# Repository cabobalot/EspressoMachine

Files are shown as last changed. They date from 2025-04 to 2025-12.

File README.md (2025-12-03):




Gagginator - A Modified Gaggia Classic Machine
==============================================
https://mrfangao.github.io/EspressoMachine/index.html

The Gagginator is a small open souce project created by The Bean Team that aims to enhance the Gaggia Classic espresso machine by replacing its traditional temperature and pressure control systems with a smart, configurable system for greater customization and consis-
tency for its users.

The project focuses on three main improvements: upgrading the temperature system with a PID controller for precise, user-adjustable temperature settings; implementing a pressure control system to allow for active profiling of extraction pressure; and adding a minimalist visual display to show real-time temperature, pressure, and brew time for easy monitoring. The system will also support custom brew settings and preset profiles based on the user’s preferences. 

## Table of Contents

- [Features](#key-features)
- [Hardware Requirements](#hardware-requirements)
- [Repository Structure](#repository-structure)
- [Files in this Repository](#files-in-this-repository)
- [Installation](#installation)
- [Usage](#usage)
- [Contributing](#contributing)
- [License](#license)

Key Features
-----------------

- **PID Temperature Control**: Precise, user-adjustable temperature control
- **Active Pressure Profiling**: Dynamic control of brew pressure during the brew cycle
- **Real-Time Monitoring**: Live display of temperature, pressure, and brew time.
- **Custom Brew Profiles**: Save and recall personalized brewing settings.
- **Web Interface**: Local webpage for detailed brew data visualization
- **Minimalist OLED Display**: Clear at-a-glance brewing information

Hardware Requirements
--------------------

- Gaggia Classic espresso machine
- ESP32-WROOM-32 dev board
- Additional components (see BOM)

<!--TODO-->

## Repository Structure
```
gagginator/
├── README.md                    
├── Espresso Machine/            
│   ├── data/
│   │   └── brewData.html      
│   ├── bitmaps.h               
│   ├── dataWebPage.cpp    
│   ├── dataWebPage.h     
│   ├── EspressoMachine.h   
│   ├── EspressoMachine.ino     
│   ├── menu.cpp     
│   ├── menu.h         
│   ├── pins.h                  
│   ├── pressure_control.cpp   
│   ├── pressure_control.h 
│   ├── pressure_sensor.cpp    
│   ├── pressure_sensor.h 
│   ├── psm.cpp    
│   ├── psm.h             
│   ├── temp_sensor.cpp      
│   ├── temp_sensor.h   
│   ├── tempControl.cpp    
│   ├── tempControl.h     
│   └── timingTestDebug.h       
├── Gaggia Schematic/                                  
```

Files in this Repository
------------------------

#### README.md 

You are currently here.

#### Espresso Machine

This folder holds the required code to run the Gagginator. All the `.cpp` and `.ino` files require their supporting `.h` files in order to run.

| File | Description |
| --- | --- |
| `data`  | A folder containing `brewData.html` for the data webpage  |
| `bitmaps.h`  | Holds the animations for coffee graphics  |
| `dataWebPage.cpp`  | The locally hosted webpage displaying brew parameters  |
| `EspressoMachine.ino` | The Main loop  of the Gagginator  |
| `menu.cpp`  | Handles all the screen and interface with the user |
| `pins.h`  | Defines the pin locations on the ESP32  |
| `pressure_control.cpp`  | Controls the pressure of the machine  |
| `pressure_sensor.cpp`  | Collects data from the pressure sensor  |
| `psm.cpp`  | Implements a PSM controller using zero-cross detection |
| `temp_sensor.cpp`  | Collects data from the temperature sensor  |
| `tempControl.cpp`  | Controls the temperature of the machine |
| `timingTestDebug.h`  | Debug code to track timing of code chunks  |

Simply copy all of the files from this folder into your project.

#### Gaggia Schematic

The circuit diagram for wiring the hardware components for the Gagginator.

Installation 
---------------

### Prerequisites

- Arduino IDE (version 1.8.x or 2.x)
- ESP32 board support package
- Required libraries:
  - Adafruit SSD1306 (for OLED display)
  - Wifi (depricated)
  <!--all other stuff sensors... TODO-->

### Steps

1. **Clone the repository**
```bash
   git clone https://github.com/yourusername/gagginator.git
   cd gagginator
```

2. **Install required libraries**
   - Open Arduino IDE
   - Navigate to Sketch → Include Library → Manage Libraries
   - Install required dependencies listed above

3. **Configure hardware pins**
   - Follow `pins.h` to match the ESP32 board and wiring configuration
   - Verify sensor pin assignments

4. **Upload the code**
   - Open `Espresso Machine/EspressoMachine.ino` in Arduino IDE (or have it configured in VSCode)
   - Select your ESP32 board from Tools → Board
   - **ENSURE** memory partition scheme is 3MB/SPIFFS no OTA
   - Select the correct COM port
   - Click Upload

5. **Upload web interface files**
   - Install the ESP32 filesystem uploader plugin
   - Upload the `data/` folder to SPIFFS/LittleFS

## Usage

### First-Time Setup

1. Power on the modified Gagginator
2. <!-- TODO -->

5. (Optional) Connect to the Gagginator WiFi access point
Navigate to the web interface at `http://192.168.4.1`

### Basic Operation

- **Temperature Control**: Use the menu to set your desired brew temperature
- **Pressure Profiling**: Select or create custom pressure profiles
- **Monitoring**: View real-time parameters on the OLED display
- **Data Logging**: Access detailed brew statistics via an browser under the AP "Gagginator" at the IP address of `192.168.4.1`.

#### Safety Notes

⚠️ **WARNING**: This modification involves working with  electricity, high temperatures, and hot water! Only attempt if you have appropriate electrical and mechanical knowledge. Improper installation may result in electric shock, fire, or equipment damage, and even injury or death

Contributing
---------------

This project is fully developed as of the release of this project. However contributions are welcome, and further modifications are at your descretion. To do so, please:

1. Fork the repository
2. Create a feature branch (`git checkout -b feature/improvement`)
3. Commit your changes (`git commit -am 'add your feature'`)
4. Push to the branch (`git push origin feature/improvement`)
5. Open a Pull Request

License
-----------

This project is open source. Specific license TBD

## Acknowledgments

The Bean Team would like to thank Samuel Bona for suffering statistical shambles and chemistry chaos. We also thank our Lord and Savior, the coffee god: James Hoffmann.

## Contact

For questions, issues, or contributions, please open an issue on GitHub.

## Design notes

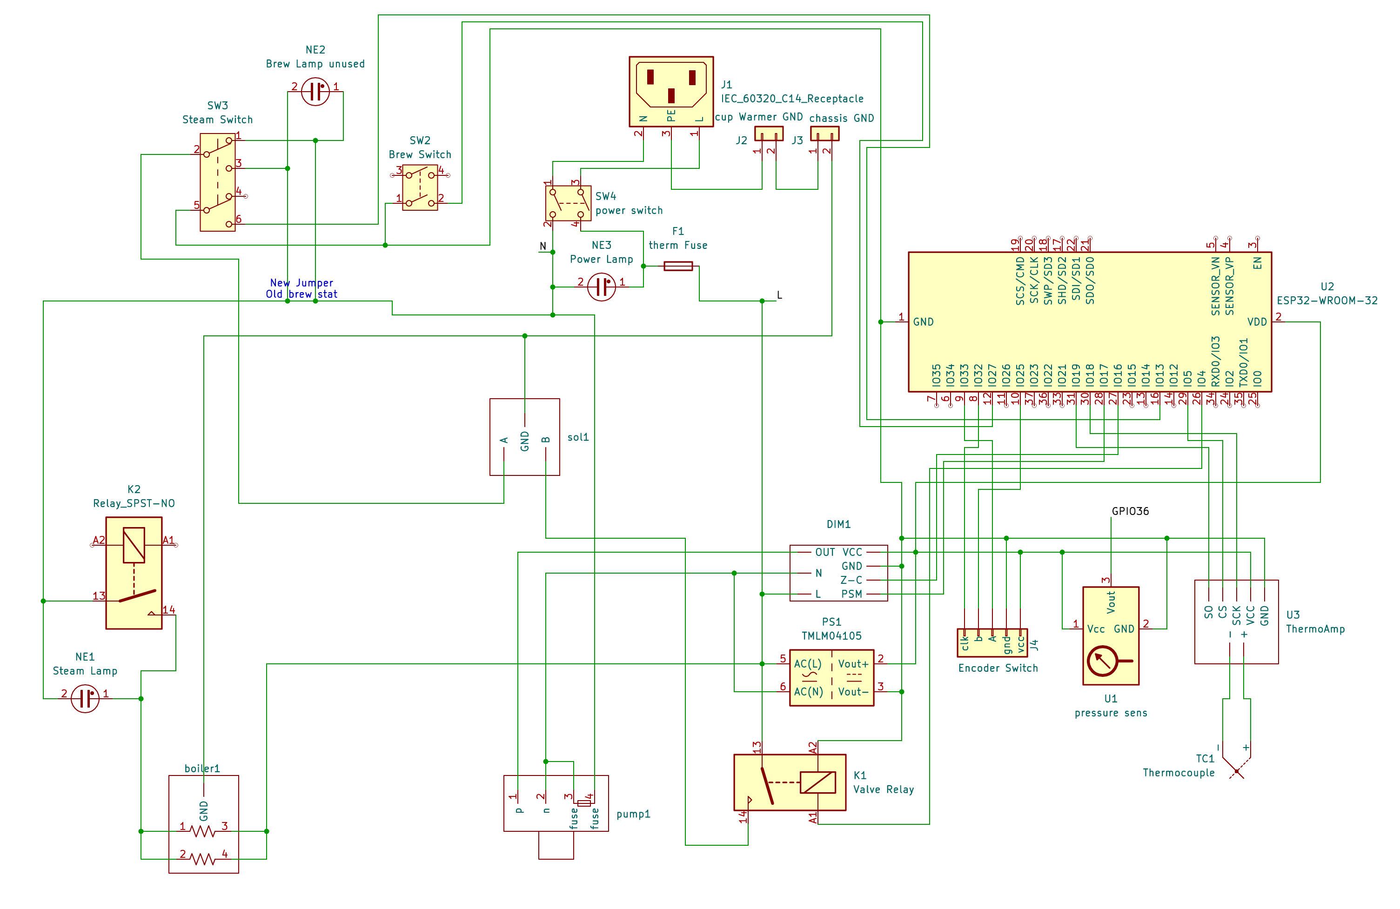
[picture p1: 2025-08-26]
schematic.png

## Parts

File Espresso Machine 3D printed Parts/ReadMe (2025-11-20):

This folder contains the stl and bambulab files used in this project.

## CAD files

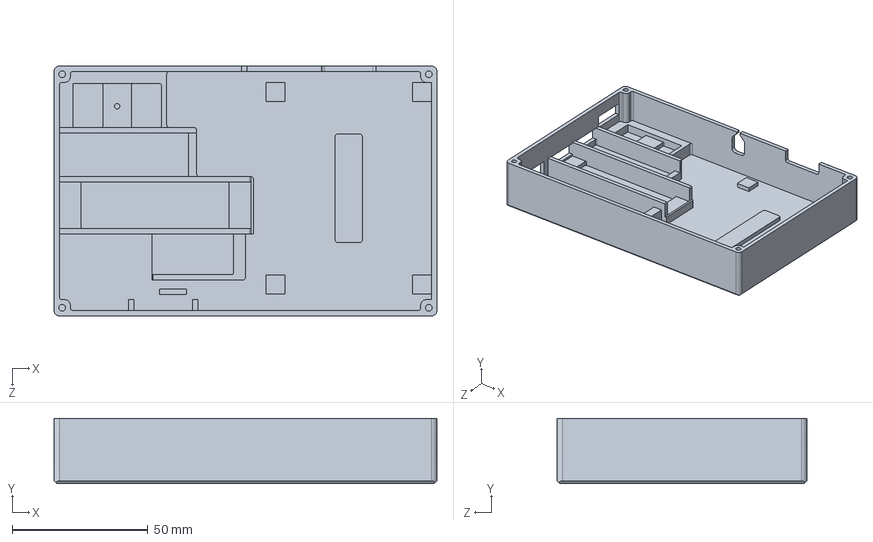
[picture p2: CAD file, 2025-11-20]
Espresso Machine 3D printed Parts/ESP32 Housing Final.SLDPRT
141.0 x 24.0 x 92.0 mm

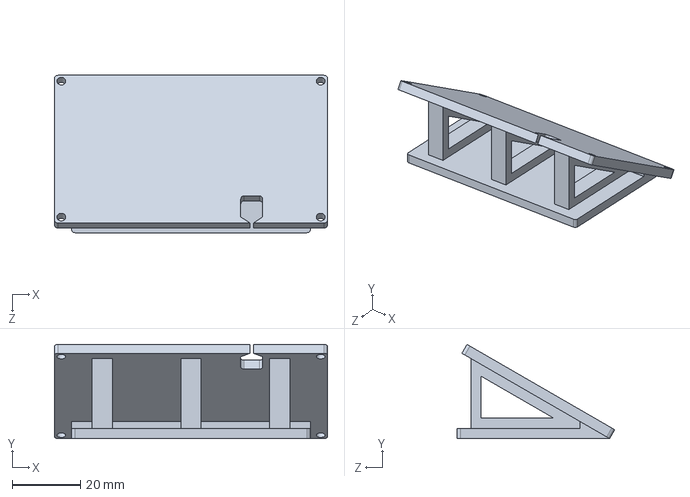
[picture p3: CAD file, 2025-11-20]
Espresso Machine 3D printed Parts/Mount for Knob and Screen Enclousure Final.SLDPRT
80.0 x 27.6 x 46.2 mm

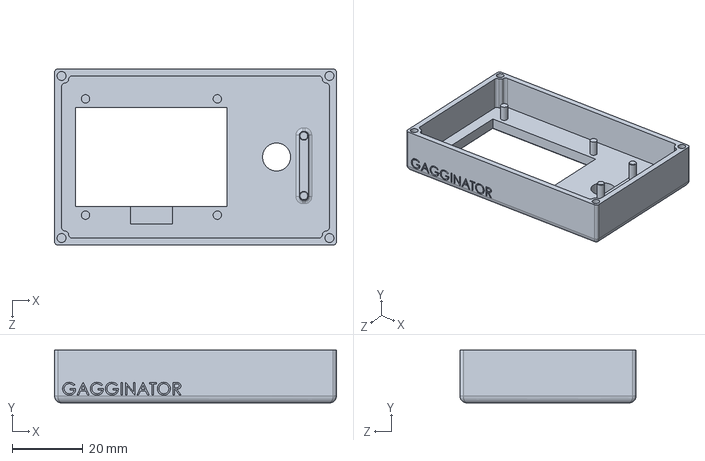
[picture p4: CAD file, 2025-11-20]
Espresso Machine 3D printed Parts/Knob and Screen Enclosure Final.SLDPRT
80.0 x 15.0 x 50.0 mm

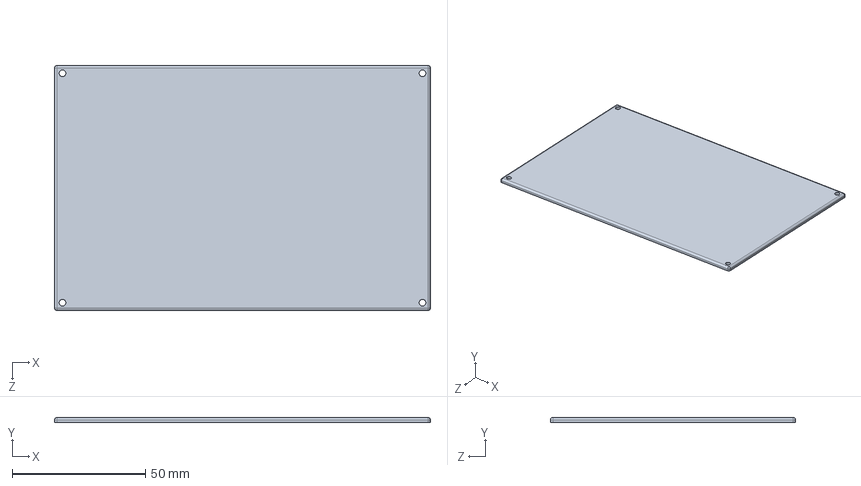
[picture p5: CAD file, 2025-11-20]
Espresso Machine 3D printed Parts/ESP32 Housing Lid Final.SLDPRT
141.0 x 2.00 x 92.0 mm

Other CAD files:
Espresso Machine 3D printed Parts/ESP32 Housing Final.STL
Espresso Machine 3D printed Parts/ESP32 Housing Lid Final.STL
Espresso Machine 3D printed Parts/Knob and Screen Enclosure Final.STL
Espresso Machine 3D printed Parts/Mount for Knob and Screen Enclousure Final.STL

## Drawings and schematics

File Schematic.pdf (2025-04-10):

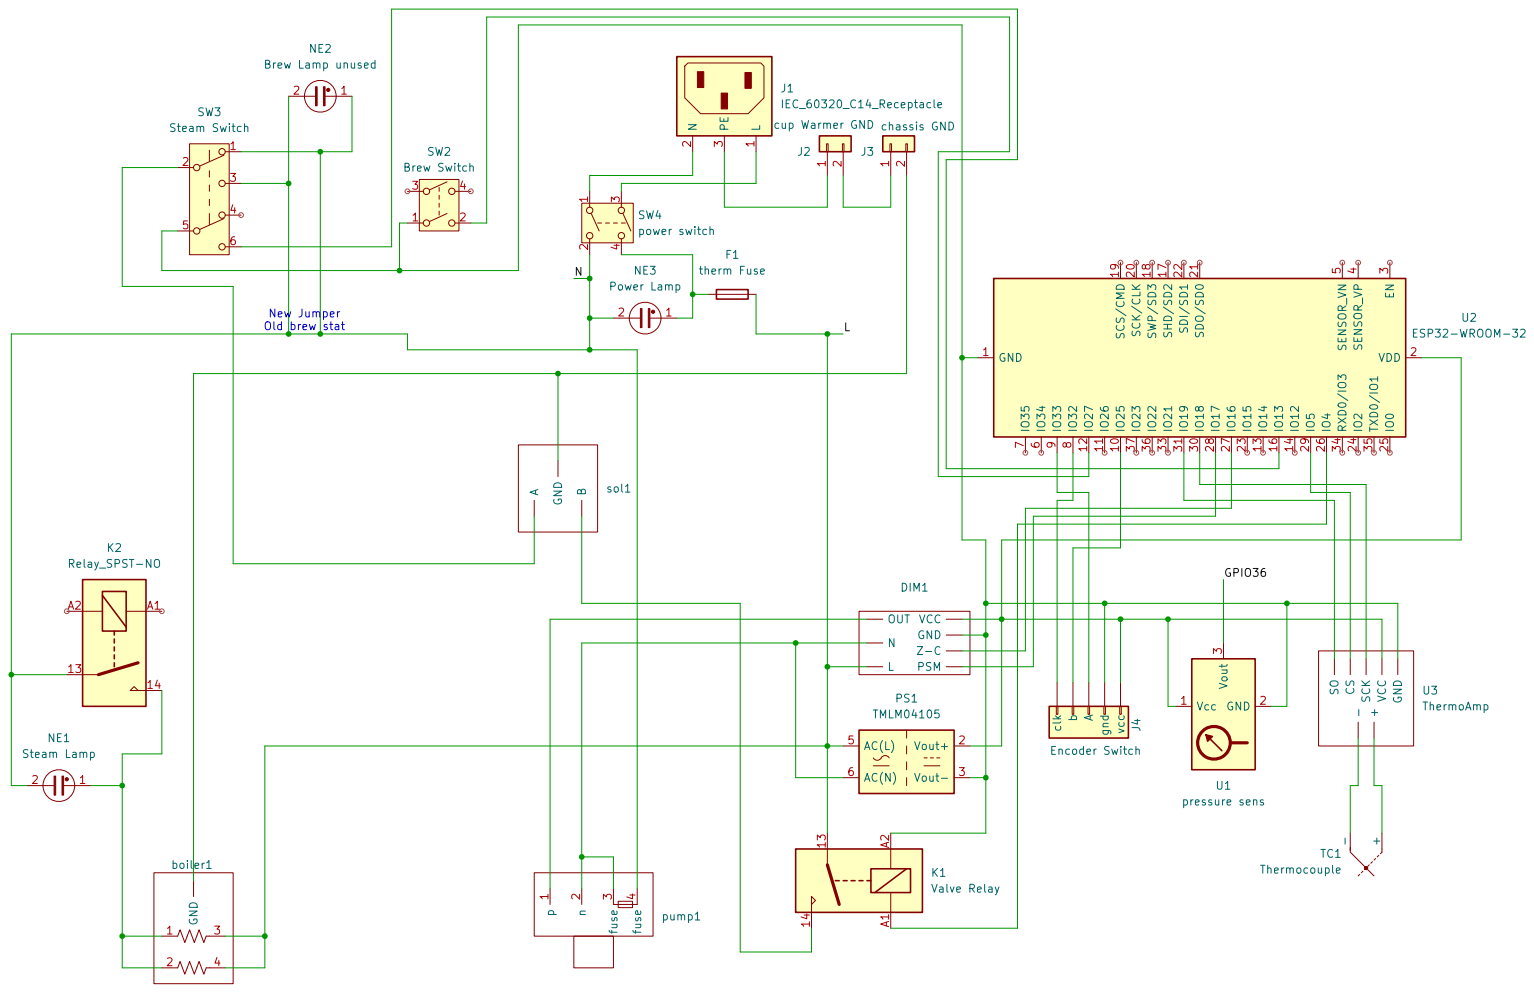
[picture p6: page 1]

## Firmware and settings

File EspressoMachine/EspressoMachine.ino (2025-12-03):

#include "Menu.h"
#include "bitmaps.h"
#include "pressure_sensor.h"
#include "temp_sensor.h"
#include "pins.h"
#include "pressure_control.h" 
#include "tempControl.h" 
#include "dataWebPage.h"
#include "EspressoMachine.h"

#include "timingTestDebug.h"


#define TEMPERATURE_OFFSET 7 // stock calibration offset

TemperatureSensor tempSensor;
PressureControl pc(5, 0.0, 0.1);
// also test in steam mode

TaskHandle_t mainTask;
TaskHandle_t uiTask;
TaskHandle_t screenShowTask;

void mainLoop(void * pvParameters);
void uiLoop(void * pvParameters);
void screenShowLoop(void * pvParameters);

static volatile float targetTemperature = 95;
static volatile float targetPressureBrew  = 120.0f;
static volatile uint8_t steamPercentage = 2;  // 1-128, default 2%
static volatile float currentTemperature = 0;
static volatile float currentPressure = 0;

static volatile float preinfusePressure = 25;
static volatile unsigned long preinfuseTime = 10;

// Brew mode pressure control: record brew start time for switching between preinfusion and normal pressure
static volatile unsigned long brewStartTimeMs = 0;
static volatile float currentTargetPressure = 0.0f;  // Currently used target pressure (for serial output)


static volatile MachineState machineState = IDLE_STATE;


void setup() {
  Serial.begin(115200);

  if (!menu.begin()) { // doing this here so we have serial if it fails
    Serial.println(F("SSD1306 allocation failed"));
    for(;;);
  }
  
  dataWebPage::init(); // I hope this doesnt care which core it happens on

  xTaskCreatePinnedToCore(uiLoop, "uiLoop", 10000, NULL, 1, &uiTask, 1);
  xTaskCreatePinnedToCore(mainLoop, "mainLoop", 10000, NULL, 1, &mainTask, 1);
  xTaskCreatePinnedToCore(screenShowLoop, "screenShowLoop", 10000, NULL, 1, &screenShowTask, 0);
}

void screenShowLoop(void * pvParameters) {
  for(;;) {
    menu.show();
    vTaskDelay(50 / portTICK_PERIOD_MS); // 20 FPS max
  }
}

void uiLoop(void * pvParameters) {
  // --- debounce state ---
  static bool     lastBrewRaw  = false,  brewStable  = false;
  static bool     lastSteamRaw = false,  steamStable = false;
  static uint32_t brewEdgeMs   = 0,      steamEdgeMs = 0;
  const  uint16_t DEBOUNCE_MS  = 30;

  menu.beginInput(PIN_KNOB_ROTATE_A, PIN_KNOB_ROTATE_B, PIN_KNOB_BUTTON); // pins an interrupt on this core

  pinMode(PIN_SWITCH_BREW, INPUT_PULLUP);
  pinMode(PIN_SWITCH_STEAM, INPUT_PULLUP);

  // Load saved settings
  menu.loadSettings();

  for(;;) {
    // ===================== UI input & rendering =====================

    menu.pollInput();
    
    int step = menu.consumeStep();
    if (step != 0) menu.moveSelection(step > 0);
    if (menu.consumeClick()) menu.select();

    // Targets from UI
    // Select corresponding temperature based on current mode
    if (machineState == STEAM_STATE) {
      targetTemperature = menu.getTargetTemperatureSteam() + TEMPERATURE_OFFSET;
    } else {
      // BREW_STATE, IDLE_STATE, HOT_WATER_STATE use brew temperature
      targetTemperature = menu.getTargetTemperatureBrew() + TEMPERATURE_OFFSET;
    }
    targetPressureBrew  = menu.getTargetPressureBrew();
    steamPercentage = menu.getSteamPercentage();
    preinfusePressure   = menu.getPreinfPressure(); 
    preinfuseTime       = menu.getPreinfTimeSec();

    // Live values back to UI
    menu.setCurrentTemperature(currentTemperature - TEMPERATURE_OFFSET);
    menu.setCurrentPressure(currentPressure);

    // ===================== Switch handling (level-based, both edges) =====================
    // Active-low hardware switches: LOW = pressed
    bool rawBrew  = !digitalRead(PIN_SWITCH_BREW);
    bool rawSteam = !digitalRead(PIN_SWITCH_STEAM);
    uint32_t now  = millis();

    // --- Brew debounce ---
    if (rawBrew != lastBrewRaw) { lastBrewRaw = rawBrew; brewEdgeMs = now; }
    if ((now - brewEdgeMs) >= DEBOUNCE_MS && rawBrew != brewStable) {
      brewStable = rawBrew;
    }

    // --- Steam debounce ---
    if (rawSteam != lastSteamRaw) { lastSteamRaw = rawSteam; steamEdgeMs = now; }
    if ((now - steamEdgeMs) >= DEBOUNCE_MS && rawSteam != steamStable) {
      steamStable = rawSteam;
    }

    // --- Unified decision (priority: BOTH -> WATER, else single) ---
    MachineState nextState = machineState;
    if (brewStable && steamStable) {
      nextState = HOT_WATER_STATE;            // Water mode: both keys pressed
    } else if (brewStable) {
      nextState = BREW_STATE;                 // Only Brew key pressed
    } else if (steamStable) {
      nextState = STEAM_STATE;                // Only Steam key pressed
    } else {
      nextState = IDLE_STATE;                 // Neither pressed
    }

    // --- Apply transition once (and set the correct page) ---
    if (nextState != machineState) {
      machineState = nextState;

      switch (machineState) {
        case BREW_STATE:
          brewStartTimeMs = millis();  // Record brew start time
          menu.setState(BREW_PAGE);
          menu.resetBrewAnimation();
          break;
        case STEAM_STATE:
          menu.setState(STEAM_PAGE);
          break;
        case HOT_WATER_STATE:
          menu.setState(WATER_PAGE);          // Both keys pressed -> enter Water page
          break;
        case IDLE_STATE:
        default:
          menu.setState(MAIN_MENU);
          break;
      }
    }

    // yield();
    vTaskDelay(20 / portTICK_PERIOD_MS); // 

  }
}

void mainLoop(void * pvParameters) {
  //temperature
  tempControl::init();
  //presure
  pinMode(PIN_PRESSURE_SENSE, INPUT);
  pc.init(PIN_DIMMER_CONTROL, PIN_DIMMER_ZERO_CROSS); // this pins an interrupt to this core

  // init
  pc.setAlwaysOff();

  pinMode(PIN_SOLENOID, OUTPUT);
  digitalWrite(PIN_SOLENOID, LOW);


  for(;;) {
    switch (machineState) {
    case IDLE_STATE:
      pc.setAlwaysOff();
      digitalWrite(PIN_SOLENOID, LOW);
      currentTargetPressure = 0.0f;
      break;
    case BREW_STATE:
      {
        // Calculate brew elapsed time (milliseconds)
        unsigned long brewElapsedMs = millis() - brewStartTimeMs;
        unsigned long preinfuseTimeMs = preinfuseTime * 1000;  // Convert to milliseconds
        
        // Use preinfusion pressure (20 PSI) for first 5 seconds, then use 70 PSI
        if (brewElapsedMs < preinfuseTimeMs) {
          currentTargetPressure = preinfusePressure;  // 20 PSI
        } else {
          currentTargetPressure = targetPressureBrew;  // Switch to 70 PSI after 5 seconds
        }
        
        pc.setSetpoint(currentTargetPressure);
        digitalWrite(PIN_SOLENOID, HIGH);
      }
      break;
    case STEAM_STATE:
      // Steam mode uses percentage for direct control, doesn't use PID
      pc.setPercentage(steamPercentage);
      digitalWrite(PIN_SOLENOID, LOW);
      // currentTargetPressure is for display, can be set to percentage value (optional)
      currentTargetPressure = (float)steamPercentage;  // Display percentage value
      break;
    case HOT_WATER_STATE:
      pc.setAlwaysOn();
      digitalWrite(PIN_SOLENOID, LOW);
      break;
    }

    tempControl::setSetpoint(targetTemperature); // screen returns a different temperature for each mode
    currentTemperature = tempControl::getTemperature();

    currentPressure = pc.getPressure();

    pc.update();

    tempControl::update();

    dataWebPage::update(currentTemperature - TEMPERATURE_OFFSET, currentPressure, targetTemperature - TEMPERATURE_OFFSET, currentTargetPressure, machineState);
    
    static unsigned long timeLastPrint = 0;
    if (millis() - timeLastPrint >= 1000) {
      timeLastPrint = millis();

      // Serial.printf("temp:%.1f, tempset:%.1f, pres:%.1f, pressSet:%.1f\r\n", currentTemperature, targetTemperature, currentPressure, targetPressure);


      // Serial.print(">temp:");
      // Serial.print(currentTemperature, 2);
      // Serial.print(",tempset:");
      // Serial.print(targetTemperature, 2);
      // Serial.print(",pres:");
      // Serial.print(currentPressure, 2);
      // Serial.print(",pressSet:");
      // Serial.print(targetPressureBrew, 2);
      // Serial.print(",targetPress:");
      // Serial.println(currentTargetPressure, 2);

      // Serial.print("UI core: ");
      // Serial.print(xTaskGetCoreID(uiTask));
      // Serial.print(" main core: ");
      // Serial.println(xTaskGetCoreID(mainTask));

    }

    // pretty sure we dont need a taskDelay here but maybe
    yield();
  }
}

void loop() {

}

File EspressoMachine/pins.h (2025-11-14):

#ifndef PINS_H
#define PINS_H

#define PIN_TEMP_SENS_SCK 18 
#define PIN_TEMP_SENS_CS  5
#define PIN_TEMP_SENS_SO  19

#define PIN_PRESSURE_SENSE 36 // analog input

#define PIN_DIMMER_ZERO_CROSS 16
#define PIN_DIMMER_CONTROL    17 // triac output

#define PIN_SCREEN_SDA 21
#define PIN_SCREEN_SCL 22

#define PIN_KNOB_BUTTON 32
#define PIN_KNOB_ROTATE_A 33
#define PIN_KNOB_ROTATE_B 25

#define PIN_SOLENOID 4
#define PIN_HEATER   26

#define PIN_SWITCH_BREW  27
#define PIN_SWITCH_STEAM 13

#endif

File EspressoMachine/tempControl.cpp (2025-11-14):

#include <Arduino.h>
#include "tempControl.h"
#include <PID_v1.h> // PID library
#include "driver/mcpwm.h" // ESP32 PWM library
#include "soc/mcpwm_periph.h"
#include "pins.h"

#define PWM_FREQ 1 // Frequency of PWM pin (1Hz)

// Static variables to hold current temp and target
static double currentTemp = 0.0;
static double setpoint = 0.0;
static double outputDuty= 0.0;

// PID varibles
static double Kp = 7.0, Ki = 1.5, Kd = 4.0;

// Delay between updates (1 sec)
unsigned long prevMillis = 0;
const unsigned long interval = 1000;

// PID object from library
static PID tempPID(&currentTemp, &outputDuty, &setpoint, Kp, Ki, Kd, DIRECT);

/*
Setup to allow for the temperature control to change the temperature
*/
void tempControl::init() {

  // PID setup
  tempPID.SetMode(AUTOMATIC);
  tempPID.SetOutputLimits(0, 100);  // clamp output

  // PWM setup
  mcpwm_timer_set_resolution(MCPWM_UNIT_0, MCPWM_TIMER_1, 60000);

  // Config to setup the PWM for the ESP32
  mcpwm_gpio_init(MCPWM_UNIT_0, MCPWM1A, PIN_HEATER);
  mcpwm_config_t pwm_config;
  pwm_config.frequency = PWM_FREQ;
  pwm_config.cmpr_a = 0.0;
  pwm_config.counter_mode = MCPWM_UP_COUNTER;
  pwm_config.duty_mode = MCPWM_DUTY_MODE_0;
  mcpwm_init(MCPWM_UNIT_0, MCPWM_TIMER_1, &pwm_config);
}

/*
Setter for the desired setpoint
*/
void tempControl::setSetpoint(float temp){
  setpoint = temp;
}

/*
Setter for the current temperature
*/ 
void tempControl::setCurrentTemp(float temp){
  currentTemp = temp;
}

/*
Controls and updates the duty cycle to reach the setpoint
*/
void tempControl::setTemperature(float tempSetpoint) {
  // PID controller
  if(tempPID.Compute()) {
    // Changes the duty cycle
    mcpwm_set_duty(MCPWM_UNIT_0, MCPWM_TIMER_1, MCPWM_OPR_A, outputDuty);
  }
}

/*
Getter for temperature
*/
float tempControl::getTemperature() {
  return currentTemp;
}

/*
Getter for setpoint
*/ 
float tempControl::getSetpoint(){
  return setpoint;
}

/*
At given intervals gets the current temperature and updates it until the 
set temperature is reached.
*/
void tempControl::update() {

    unsigned long currMillis = millis();

    if(currMillis - prevMillis >= interval) { // Delay 
      prevMillis = currMillis;

      currentTemp = TemperatureSensor::getTemperature(); // Grab the current temperature
      
      tempControl::setTemperature(setpoint); // Reach that temperature

    }
}

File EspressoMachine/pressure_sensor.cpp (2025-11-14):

#include <Arduino.h>
#include "pressure_sensor.h"
#include"pins.h"

// Sensor parameters
const int pressurePin = PIN_PRESSURE_SENSE;
const float sensorMinVoltage = 0.5;
const float sensorMaxVoltage = 4.5;

const float pressureMin = 0.0;
const float mPaMax = 1.2;

// ESP32 specific parameters
const float maxVoltage = 3.3;
const float adcResolution = 4095.0; // 12 bit resolution (0-3.3V)

// Voltage divider parameters
const float voltageDividerRatio = 1.515;

// Averaging constant
static const uint8_t NUM_READINGS = 20;
static uint16_t ringBuf[NUM_READINGS];  // ~40B
static uint8_t  head = 0;               // Next location to write to
static uint8_t  count = 0;              // Current number of samples (<= NUM_READINGS)
static uint32_t sumAdc = 0;             // Run and prevent overflow

/*
Averages the pressure readings coming in from the sensor
*/
static inline uint16_t readAveragedAdc() {
  uint16_t newv = (uint16_t)analogRead(pressurePin);
  if (count < NUM_READINGS) {
    // Buffer not full, accumulate directly
    sumAdc += newv;
    ringBuf[head++] = newv;
    count++;
    if (head == NUM_READINGS) head = 0;
  } else {
    // Buffer full, pop the old value, add the new one in
    uint16_t oldv = ringBuf[head];
    sumAdc += newv;
    sumAdc -= oldv;
    ringBuf[head] = newv;
    head++;
    if (head == NUM_READINGS) head = 0;
  }

  // Calculate the current average (rounded)
  uint32_t denom = (count == 0) ? 1 : count;
  uint16_t avg = (uint16_t)((sumAdc + denom / 2) / denom);
  return avg;
}

/*
Handles the calculations to take voltage sensor readings into a pressure format.
*/
int calculatePressure() {
  int i = 0;
  int rawTotalValue = 0;
  static int avgValue;
  static float bar = 0;
  static float psi = 0;
  static unsigned long prevMs_ = 0;

  const unsigned long now = millis();

  // update every 3ms
  if (now - prevMs_ >= 3) {
    prevMs_ = now;

    avgValue = readAveragedAdc();
    // Convert ADC value to ESP pin voltage (0-3.3V)
    float measuredVoltage = (avgValue / adcResolution) * maxVoltage;
    
    // Calculate the actual sensor output voltage (accounting for voltage divider)
    float actualVoltage = measuredVoltage * voltageDividerRatio;
    
    // Scale the reading to actual pressure in MPa
    float pressureRange = mPaMax - pressureMin;
    float voltageRange = sensorMaxVoltage - sensorMinVoltage;
    
    float pressure = ((actualVoltage - sensorMinVoltage) * pressureRange / voltageRange) + pressureMin; // in mPa
    
    // Ensure pressure is within expected range (sanity check)
    pressure = constrain(pressure, pressureMin, mPaMax);

    // Conversion to bar and PSI
    bar = pressure * 10;
    psi = pressure * 145.038;
  }
  return psi; // PSI is default, but mPa or bar is valid.
}

const int printToPlotter = 0; // 1 to plot, 0 to print metadata

/*
Prints data either to a serial plotter or directly into the console
*/
void printAvgData(float avgSensorValue, float avgPsi, float avgBar, float avgVoltage) {
  if (printToPlotter) {
    Serial.println(avgPsi); // fill with desired measurement
  }
  else { // Print to console
    Serial.print("Raw ADC: ");
    Serial.println(avgSensorValue);
    Serial.print("Measured Voltage: ");
    Serial.println(avgVoltage, 3);
    Serial.print("Bar: ");
    Serial.println(avgBar, 3);
    Serial.print("PSI: ");
    Serial.println(avgPsi, 3);
  }
}

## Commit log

2025-04-02 Working Arduino Pressure Sensor Code
2025-04-03 pressure code on ESP32 with Voltage Divider
2025-04-08 Rough Skeleton code for pressure control
2025-04-08 temperature ESP32 read code
2025-04-10 start schematic
    [GaggiaSchematic.kicad_pcb, GaggiaSchematic.kicad_sch]
2025-04-10 schematic v1
    [GaggiaSchematic.kicad_sch]
2025-04-10 added .h and .cpp files for sensors
2025-04-15 fix the psm lib
    [psm.cpp]
2025-08-26 temperature header
2025-08-26 pressure headers
2025-08-28 Implementing Untested Temperature Control
2025-08-28 Move Encoder to menu
2025-09-02 Fixed PWM Generation
2025-09-02 Pressure Control not tested
2025-09-02 Updated PWM to be 1Hz
2025-09-03 rework temperature sensor, and more tests
2025-09-06 fixed to make pressure sense non-blocking.
    [pressure_sensor.cpp]
2025-09-06 slight correction of averaging timing
    [pressure_sensor.cpp]
2025-09-16 Updated tempControl PID values
2025-10-02 new PID values
2025-10-02 pressure pid tuned slightly better
2025-10-11 initial datawebpage, no sensor reads
2025-10-11 can now only read and graph sensor values
2025-10-13 Control state added
    Haven’t tested
2025-10-28 Fix update problem
    Last Version have some problem in main loop
    [Menu.h, menu.cpp, pins.h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]
2025-10-30 Standatrdize pin definitions
2025-11-11 added timer
2025-11-11 new thread for faster UI
2025-11-14 new encoder
2025-11-14 show correct setpoint on webpage
    [EspressoMachine.ino]
2025-11-14 Added comments for pressure sensor
2025-11-14 added comments for temperature sensor
2025-11-20 Create folder for #D printed parts
2025-11-25 Fix resetting internal counters too often
    [psm.cpp]
2025-12-03 added PCB files
    [copper_bottom.gbr, copper_top.gbr, drill_1_16.xln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]
2025-12-03 fix temperature offset
2025-12-03 steam pressure to % conversion wasnt working, using default values instead.

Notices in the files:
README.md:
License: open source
